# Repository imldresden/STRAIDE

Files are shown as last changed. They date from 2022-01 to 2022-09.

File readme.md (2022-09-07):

# STRAIDE: A Research Platform for Shape-Changing Spatial Displays based on Actuated Strings

**[Severin Engert](https://imld.de/en/our-group/team/severin-engert/), [Konstantin Klamka](https://imld.de/en/our-group/team/konstantin-klamka/), [Andreas Peetz](https://imld.de/en/our-group/team/andreas-peetz/), [Raimund Dachselt](https://imld.de/en/our-group/team/raimund-dachselt/)**

**[Interactive Media Lab Dresden](https://imld.de/en/)**

## CHI'22 Full Paper

We present STRAIDE, a string-actuated interactive display environment that allows to explore the promising potential of shape-changing interfaces for casual visualizations.
At the core, we envision a platform that spatially levitates elements to create dynamic visual shapes in space.
We conceptualize this type of tangible midair display and discuss its multifaceted design dimensions.
Through a design exploration, we realize a physical research platform with adjustable parameters and modular components.
For conveniently designing and implementing novel applications, we provide developer tools ranging from graphical emulators to in-situ augmented reality representations. 
To demonstrate STRAIDE's reconfigurability, we further introduce three representative physical setups as a basis for situated applications including ambient notifications, personal smart home controls, and entertainment.
They serve as a technical validation, lay the foundations for a discussion with developers that provided valuable insights, and encourage ideas for future usage of this type of appealing interactive installation.

[doi.org/10.1145/3491102.3517462](https://doi.org/10.1145/3491102.3517462)

## Repository
maintained by [Severin Engert](https://github.com/sev01)

### Components:
* [Hardware](Hardware)
* [Firmware](Firmware)
  * [Server](Firmware/Server_NodeJS)
  * [Slave Motors](Firmware/Motor_Uno)
  * [Slave Colors](Firmware/Color_ESP32)
* [Software](Software)
  * [Platform Emulator](Software/PlatformEmulator) ([Executable](Software/PlatformEmulator/PlatformEmulator.zip), [Unity-Project](Software/PlatformEmulator/Unity), AR (tba))
  * [Clients](Software/Clients) ([Arduino](Software/Clients/Arduino), [JavaScript](Software/Clients/), [C#](Software/Clients/Unity))
  * [Visual Editor](Software/VisualEditor) (live (tba))

## Contributors

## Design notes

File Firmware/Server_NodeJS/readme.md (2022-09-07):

# NodeJS Server

The central heart of STRAIDE is a NodeJS server. It handles all the communication between the Motor Towers, the Color Clients, and any application. It opens 3 separate interfaces: a TCP server on port 7778 for the communication via Ethernet with the Arduino Unos, a WS server on port 7779 for the wireless communcation with any hardware components like the color clients, and the external WS interface for applications on port 7777.
For every Motor Tower/TCP client that opens a connection to the server, it creates a new class of `Tower` including four `Elements` that handle the movement (speed, acceleration, shutdown) of the physical elements. Applications connected to the WS interface can send command according to the [Protocol](../../Hardware/protocol.md) which will control those parameters.
A loop will regularly check for changes and send out new values to the assigned Motor Tower.

## Setup
Install `NodeJS` and `npm` on a capable machine, preferable a thin client like a Raspberry Pi 4B. Then connect the machine to a local network containing all the Motor Towers via Ethernet or WiFi. Disable any other connection interface, as the server will pick the first one available. Configure your router so that your machine receives a static IP address, copy this address to the [Motor_Uno](../Motor_Uno) firmware. Finally, run `npm install` and `node controller.js` to start the server and make sure, all three interfaces are properly connected.

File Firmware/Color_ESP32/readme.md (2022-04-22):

# Color Controller

STRAIDE's Matrix Setup uses 64 illuminated elements for appealing visualizations in midair.
Each element features a single SK6812 LED for individual illumination.
All LEDs are connected to a central PCB in the lower Display Element Unit via 3m long tone arm wires.
8 LEDs make up a column, and overall 8 columns are connected to 8 digital pins of an NodeMCU ESP32.
This wifi-capable microcontroller connects to the central server and receives websocket messages containing new color information.
These are repeatedly send to the 8 strains of LEDs, and (with low latency) color works in unison with the actuation of the spheres.

## Message Format
`messageType | messageID | LED0 red | LED0 green | LED0 blue | LED0 white | LED1 red | LED1 green | ...`

`messageType`: `0x01` for new colors  
`messageID`: sequential numbers `0-255`  
LED: `index = y * DIMX + x` and `red`(byte)

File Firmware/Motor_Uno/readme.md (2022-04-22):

# Motor Controller

STRAIDE setups comprise multiple actuation towers, each with 4 motors and a PCB stack on top.
It is a stack of an Arduino Uno, an Ethernet Shield, a custom PCB to reroute pins, and an CNC Shield.
The Uno runs the software from this folder.
It uses the Ethernet Shield to connect to a network and WebSockets to connect to the central server.
Commands are mapped to the motor positions, including setup, calibration, and handling of direct user input.

## Setup
In `defines.h`, you need to adjust the `SLAVE_ADDR` for each individual actuation tower. Also, the `IPAddress serverIP(X.X.X.X)` and `IPAddress clientIP(X.X.X.X)` needs to be set up to fit the network.

## Communication
Element Position: `0x30 | messageID | M0 (high) | M0 (low) | M1 (high) | M1 (low) | M2 (high) | M2 (low) | M3 (high) | M3 (low)` (positions for each motor `M`: `high<<8+low`) 

Parameter: `0x20 | ParamID | high | low` (ParamID: `0x01`-speed, `0x02`-acceleration)

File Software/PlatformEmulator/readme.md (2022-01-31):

# Platform Emulator

The **Platform Emulator** can be used to test your applications. It emulates the full device and its behavior. Upon start, the application sets up a WebSocket server, that can be accessed from the same device or the local network. It will take and answer all incoming messages just like the original device (only low-level communication). The resultant behavior of the device is instantly visible. Use it to test your application before trying it on the real SCI.

The Platform Emulator can either be started as a standalone [Application](PlaformEmulator.zip) or opened as a [Unity Project](Unity).

## Application
The _Application_ folder contains a Windows Standalone **Simulator.exe** that can be executed. The Platform Emulator should start as a windowed application, which can be adjusted to your setup.

**Common Problems:**

1. The application sets up a WebSocket server on the localhost of your system with port 7777. If this address is already taken, the server will throw an error and the application will not start properly.
2. If you want to access the WebSocket server from your local network, the address with the assigned port needs to be accessible. Windows Firewall tends to block unknown ports. More information on how to set up inbound and outbound rules for Windows Firewall can be found [here](https://www.tomshardware.com/news/how-to-open-firewall-ports-in-windows-10,36451.html). To check for errors, run `netstat -an` in the Windows PowerShell and check for existing connections with port 7777, like 0.0.0.0:7777, _yourIP_:7777, or ::::7777.

## Unity Project
The **Unity** folder contains the full Unity project for the Platform Emulator. You should start the Unity Hub and add the folder to your projects. Select a fitting Unity Version (currently 2020.1.11f1) and open the project. The Platform Emulator can be run directly from the Unity Editor. WebSocket Server or Port problems are less common, as they are tunneled through the Unity ports 50XXX.

# Functionality
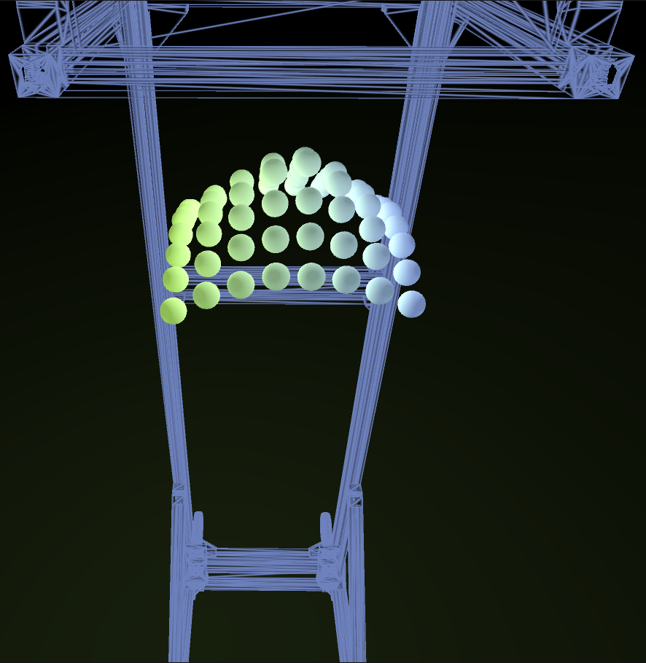
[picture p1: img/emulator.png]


The core of the Platform Emulator is the digital model of the device with its 64 spheres. Their position and color relate to the current state of the SCI which can be altered by incoming messages.

**Limitations:**
- speed parameter is approximated, slow speeds use workaround with jitter
- color rendering might be different than with the original device

## Controls
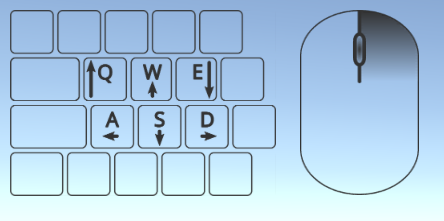
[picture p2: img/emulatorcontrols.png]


The space around the display can be navigated by using the WASD keys to move around, the QE keys to move up and down, the scroll wheel to zoom and the left mouse button to look around.

Further keys used as follows:<br/>
1,2,3,4,5 - predefined camera positions<br/>
0 - toggle frame<br/>
P - pick display<br/>
L - toggle light<br/>
O - toggle strings<br/>
ESC - exit application

## Interaction
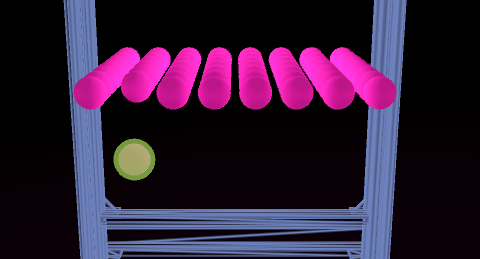
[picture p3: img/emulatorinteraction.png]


By hovering the mouse above an outer non-moving element, it gets selected. The position of a selected element can be manually altered using the primary mouse button.

## Strings
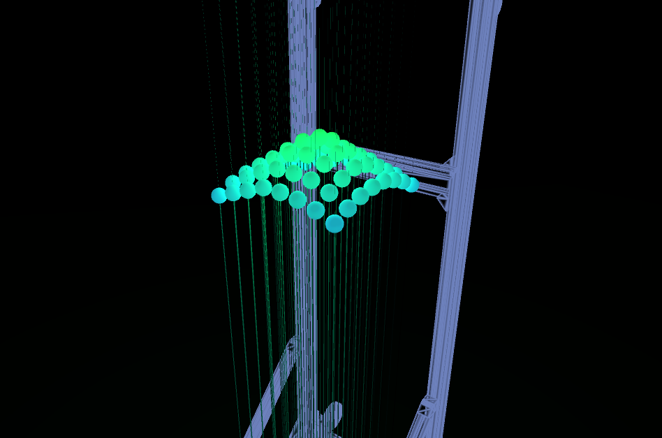
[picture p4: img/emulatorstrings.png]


Using the **O** key, strings and cables can be toggled. They are connected to each element and move in accordance, although applied line renderer is a bad approximation.

## Lights
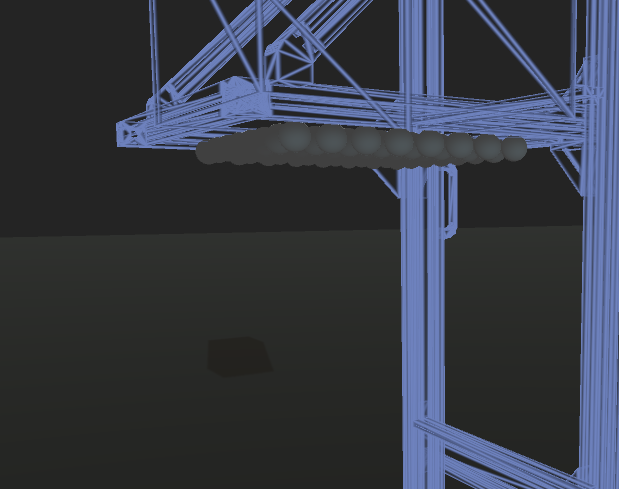
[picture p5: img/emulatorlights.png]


Using the **L** key, environmental light can be toggled for improved realism.

## Displays
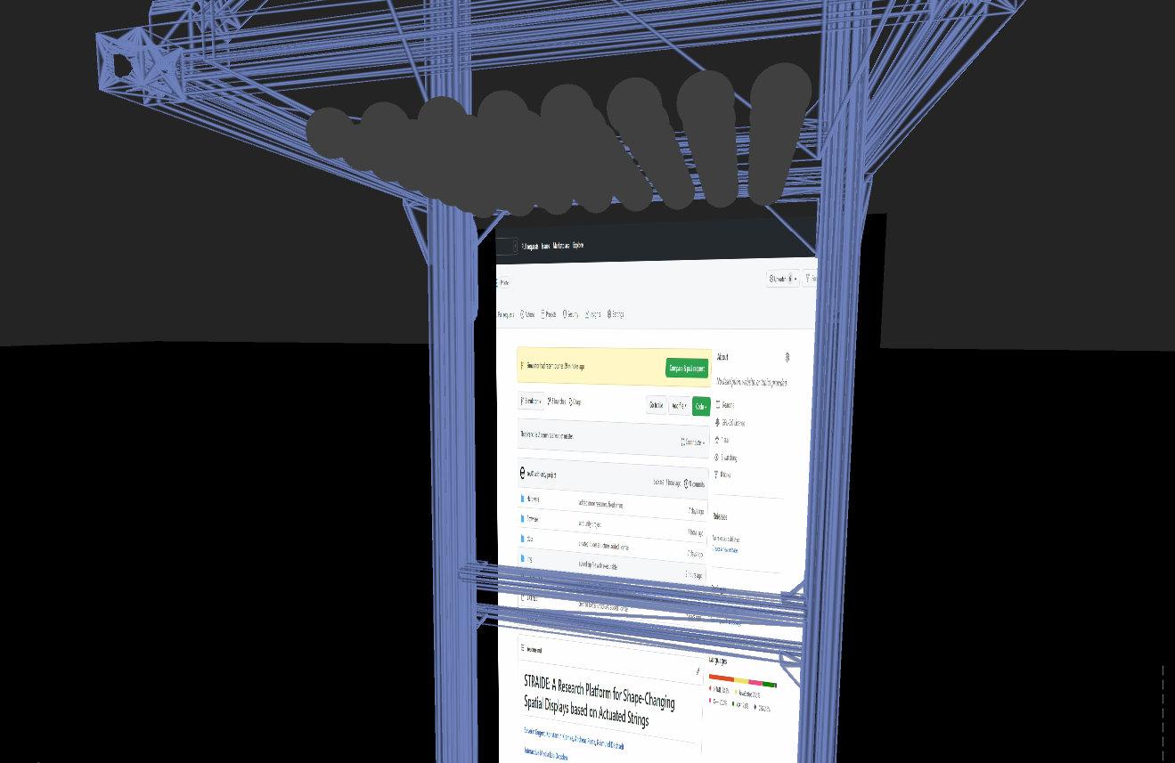
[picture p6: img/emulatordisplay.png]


For some applications, it was nice to have a background image or so inside the Platform Emulator. Therefore, it features multiple canvases to which a camera can be streamed, most often used with a virtual cam transferring parts of the screen. Use **P** to toggle the canvas.

## Supplementaries
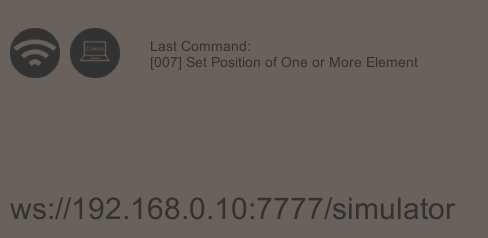
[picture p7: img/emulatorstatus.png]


Status information is displayed in the lower part of the screen.
The first icon shows the Platform Emulators connectivity. The second icon shows whether a client is connected or not. On its right, the last inbound command is displayed according to the message's ID. To learn more about the messages, see [Protocol](../../Hardware/protocol.md).
The empty space underneath the icons is filled with log/error messages, as they occur. This can be used for Debug purposes, e.g. a warning is displayed if an inbound message had the wrong length or format.

In the lower-left corner, the address of the WebSocket server is displayed. It needs to be entered into the SCIClients address field.

The lower-right corner shows the target position values for all 64 elements.

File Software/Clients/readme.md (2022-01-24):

# STRAIDE Client Libraries

To simplify the application development for STRAIDE on various platforms, we implemented client libraries in different programming languages (JS, C#, C++).They provide functions for establishing connections and setting the properties of elements, as well as events for system state changes and user input.

For further details, please take a look into the individual folders:
* [JavaScript](JS)
* [C# (for Unity)](Unity)
* [C++ (for Arduino)](Arduino)

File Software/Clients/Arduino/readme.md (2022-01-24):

# Arduino Client

This _SCIClient_ is intended to be used on ESP32 micro-controller boards that should communicate with STRAIDE, e.g., for IoT applications

## Setup

To use the SCIClient in a script, you should create a new library. Open the Arduino [Library](https://www.arduino.cc/en/Guide/Libraries) folder and create a new folder called _SCIClient_. Copy the `SCIClient.h` and `SCIClient.cpp` files into this folder. Now you need to import the library in your sketch.

The library uses the [Arduino WebSocket](https://github.com/Links2004/arduinoWebSockets) library. Make sure, the library is ready for import aswell. 

Create a new SCIClient object as a global variable with the correct address information. In your script's `setup()` function, you should setup a WiFi connection and register a callback that is triggered when the WebSocket server is ready. Use this call to request information that is needed for your application.

```cpp
#include <SCIClient.h>

SCIClient client = SCIClient("192.168.0.1", 7777, "/simulator");  // for Simulator
// SCIClient client = SCIClient("10.6.0.1", 7777, "/");  // for real STRAIDE

void setup(){
   WiFi.mode(WIFI_STA);
   WiFi.begin(WLAN_SSID, WLAN_PASS);
   client.CallOnReady(ServerIsReady);
}

void ServerIsReady(){
   sciclient.GetInformation(SCIClient::InfoID::DIM);
}
```

## Ping
Send a simple ping to the device.
```cpp
sciclient.SendPing();
```

## Acknowledgments
Typically, STRAIDE will send acknowledgment packets `0x01 | MessageID` for every received data packet. To reduce the traffic, acknowledgments can be toggled by sending:
```cpp
sciclient.ToggleAcknowledgment(false);
```

## Reset
To reset STRAIDE or some parts thereof send
```cpp
sciclient.Reset(0x00);
```
The code determines what to reset:\
`0x00` - Reset Everything\
`0x01` - Reset Elements' Positions (aka calibrate positions)\
`0x02` - Reset Elements' Color (aka turn off all lights)

## Request Information
For many client applications it is necessary to know some information about STRAIDE. The `InfoID` defines all potential information that can be requested. Currently it supports `DIM, DIAMETER, RESOLUTION, STEPSPERM, MAXSTEPS`.

```cpp
sciclient.GetInformation(SCIClient::InfoID::DIM);
```
To receive the requested information, you need to register a custom callback function. Take a look into the [Protocol](/Hardware/protocol.md) to find the encoding of the response's data.
```cpp
int maxsteps = 0;
void RequestInformation(){
   sciclient.CallOnInfo(ReceiveInformation);
   sciclient.GetInformation(SCIClient::InfoID::MAXSTEPS);
}

private void ReceiveInformation(byte[] data){
   switch(data[0]){
      case SCIClient::InfoID::MAXSTEPS:
         maxsteps = (int)word(data[1], data[2]);
         break;
   }
}
```

## Set Parameter
To set a motor parameter of STRAIDE (see [Parameters](/Hardware/parameters.md)), use
```cpp
sciclient.SetParam(SCIClient::ParamID::SPEED, 1000);
```
The `SCIClient::ParamID` currently defines `SPEED, ACCELERATION`.

## Set Position
The API provides three ways to set the position of elements. To set the position of a single element, use
```cpp
sciclient.SetElementPosition(new SCIElement(2,5), 4321);
```

To set multiple elements (in a rectangular region defined by the coordinates of the lower left and upper right corner elements) to the same position, use
```cpp
sciclient.SetAreaPosition(new SCIElement(2,3), new SCIElement(4,6), 4321);
```

To set the position of all elements individually, use
```cpp
sciclient.SetMultiplePositions(positions, 64);   // int positions[64]; 
```
The array needs to have a length of exactly `XDimension * YDimension`. To properly sort the elements' positions, calculate `i = y * XDimension + x` for each element. The second parameter needs to be the length of the array.

## Set Color
The API provides three ways to set the color of elements. A basic definition for colors is provided by the `SCIColor` class. To set the color of a single element, use
```cpp
sciclient.SetElementColor(new SCIElement(2,5), new SCIColor(255,0,0));
```
To set multiple elements (in a rectangular region defined by the coordinates of the lower left and upper right corner elements) to the same color, use
```cpp
sciclient.SetAreaColor(new SCIElement(2,3), new SCIElement(4,6), new SCIColor(255,0,0));
```

To set the color of all elements individually, use
```cpp
sciclient.SetMultipleColors(colors, 64);   // SCIColor colors[64];
```
The array needs to have a length of exactly `XDimension * YDimension`. To properly sort the elements' positions, calculate `i = y * XDimension + x` for each element.

## Set Position and Color
To reduce the WebSocket traffic, messages can combine position and color definitions for one or multiple elements. 
```cpp
sciclient.SetPositionAndColor(new SCIElement(2,5), 4321, new SCIColor(255,0,0));

sciclient.SetAreaPositionAndColor(new SCIElement(2,3), new SCIElement(4,6), 4321, new SCIColor(255,0,0));

sciclient.SetMultiplePositionsAndColors(positions, colors);
```

## Animations
Some animations are predefined on STRAIDE itself. Currently, this includes different sine waves. Each animation has an ID (currently ranging from 0-5). To start or change an animation, use
```cpp
sciclient.PlayPreset(2);
```
Animations can be stopped by sending any command that sets the positions of at least one element.

The amplitude of the predefined sine waves is approximately 20cm. But the vertical position of the sine wave can be adapted by using
```cpp
sciclient.SetOffset(4321);
```

## User Input
Users can manually drag the outer elements of the device. The respective data is send to all clients via the WebSocket broadcast method. Register a custom method using `CallOnInput(method)` to access the data. The method should take an `SCIElement` and an integer value as parameters like this:

```cpp
sciclient.CallOnInput(UserInput);

private void UserInput(SCIElement element, int value){
   // element.x and element.y available
   // value: absolute steps from top for respective element
}
```

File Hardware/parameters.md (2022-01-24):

# Controllable Motor Parameters

To date, STRAIDE applications can control 2 different parameters of the actuators.

## Speed
The speed for each motor can be defined as an unsigned integer value. It refers to the number of steps per second, which the stepper motor actuates the elements. A single step size can be calculated as

$step=pi*40mm/400\approx0.31416mm$

The real world speed can therefor be calculated like

$RealSpeed=speed*^{step}/_s$

| Speed | RealSpeed |
| --- | --- |
| 100 | $`31^{mm}/_s`$ |
| 1000 | $`314^{mm}/_s`$ |
| 4000 | $`1257^{mm}/_s`$ |

The speed value can be picked in between $0-4000$. Everything above 4000 is not achievable due to hardware constraints. Everything above 1000 is only achievable, if only one of every 4 motors is actuated, as they are internally grouped into $2\times2$ motor towers. Speeds below 200 should be prevented, as the motor's torque is reduced at low speeds.

## Acceleration
***! Acceleration NOT yet implemented in Simulator !*** 

The acceleration is also defined as an unsigned integer value. It refers to the speed increase in steps per square second. Generally an acceleration above 1000 should be picked.

More information can be found in the chart. Currently, the elements weight approximately 200g.
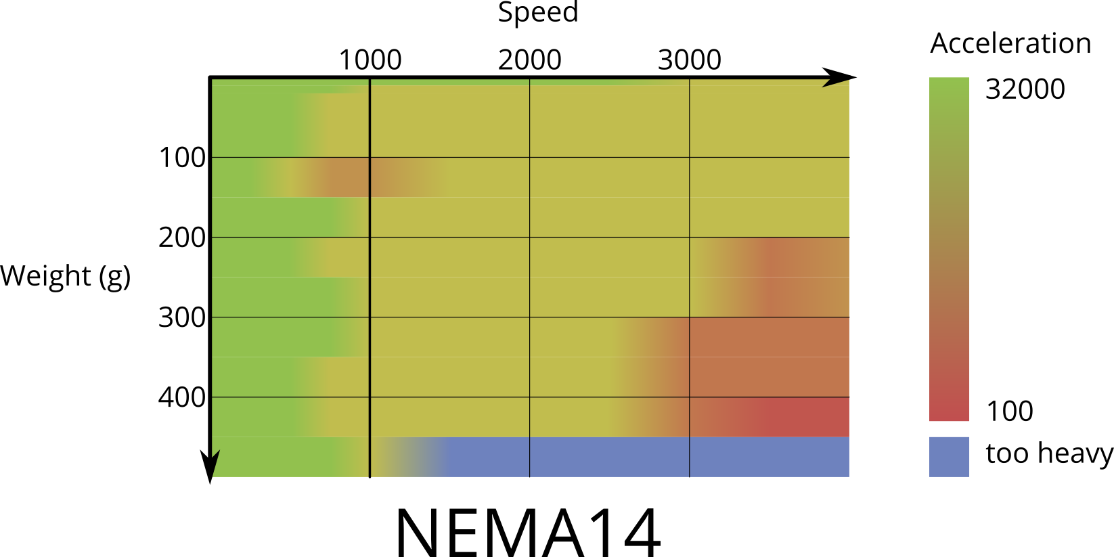
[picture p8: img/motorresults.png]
motorresults


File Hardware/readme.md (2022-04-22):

# STRAIDE Hardware

## License
Copyright Severin Engert 2022.

This source describes Open Hardware and is licensed under the CERN-OHL-S v2.
You may redistribute and modify this source and make products using it
under the terms of the [CERN-OHL-S v2](https://ohwr.org/cern_ohl_s_v2.txt).

This source is distributed WITHOUT ANY EXPRESS OR IMPLIED WARRANTY, INCLUDING OF MERCHANTABILITY, SATISFACTORY QUALITY AND FITNESS FOR A PARTICULAR PURPOSE. Please see the CERN-OHL-S v2 for applicable conditions.
Source location: [https://github.com/imldresden/STRAIDE](https://github.com/imldresden/STRAIDE)

As per CERN-OHL-S v2 section 4, should You produce hardware based on this source, You must where practicable maintain the Source Location visible on the external case of the STRAIDE or other products you make using this source.

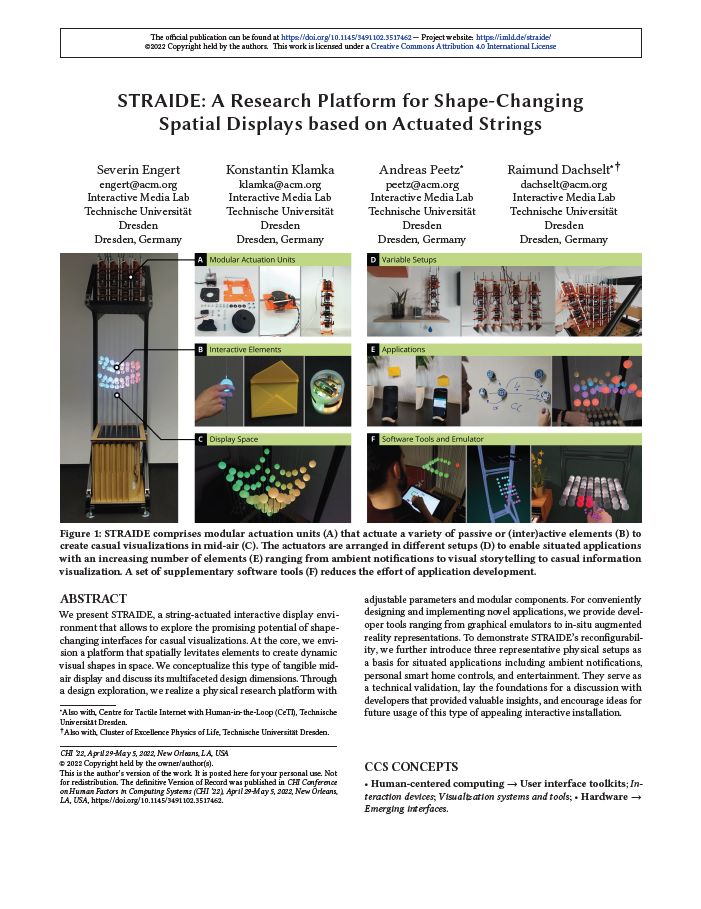
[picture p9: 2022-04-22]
docs/assets/img/full_paper.jpg

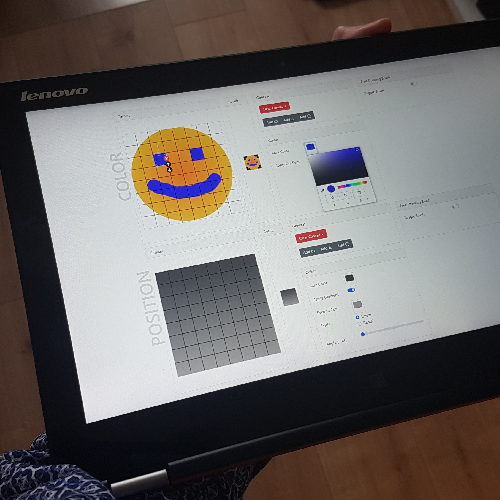
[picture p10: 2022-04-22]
docs/assets/img/visual_designer.png

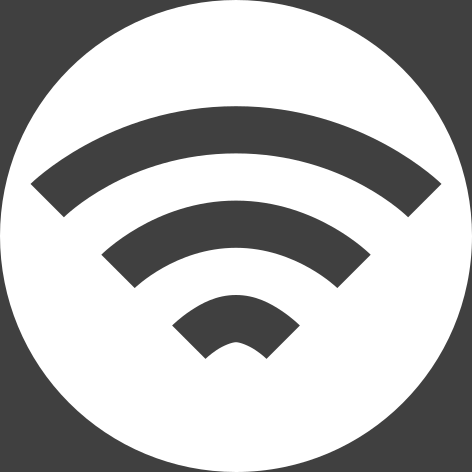
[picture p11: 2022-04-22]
Software/PlatformEmulator/Unity/Assets/Images/connected.png

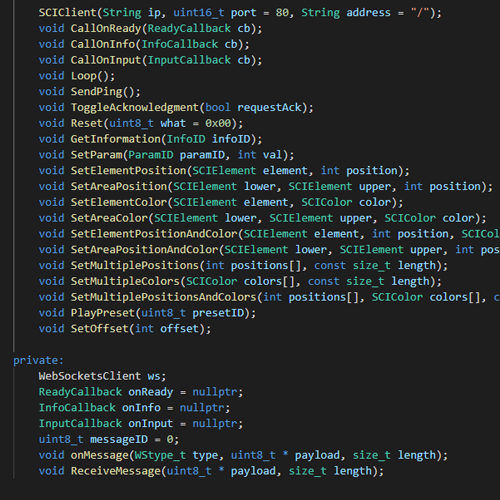
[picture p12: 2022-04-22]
docs/assets/img/clients.png

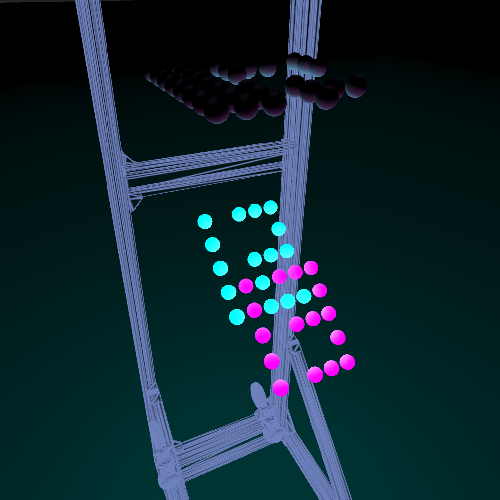
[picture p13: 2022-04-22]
docs/assets/img/emulator.png

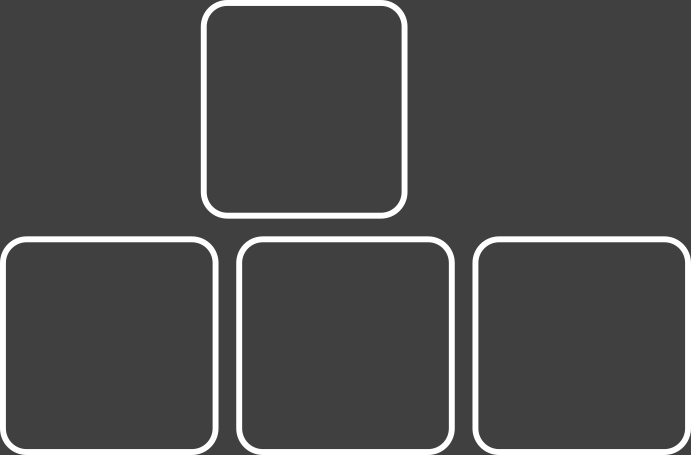
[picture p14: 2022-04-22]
Software/PlatformEmulator/Unity/Assets/Images/controls.png

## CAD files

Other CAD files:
Hardware/stl/Spool.stl
Software/PlatformEmulator/Unity/Assets/Frame.stl
Hardware/stl/EndStopHolder.stl
Hardware/Fusion360/BackCover.f3z
Hardware/Fusion360/ControllerMount.f3z
Hardware/Fusion360/LuffTackle.f3d
Hardware/Fusion360/MotorMount.f3z
Hardware/Fusion360/UpperCover.f3z

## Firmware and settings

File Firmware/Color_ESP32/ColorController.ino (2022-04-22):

#include <Adafruit_NeoPixel.h> // install library from https://github.com/adafruit/Adafruit_NeoPixel
#include <WiFi.h>              // part of esp-32 arduino library https://github.com/espressif/arduino-esp32
#include <confidential.h>      // private libray containing WLAN_SSID and WLAN_PASS
#include <WebSocketsClient.h>  // install library from https://github.com/Links2004/arduinoWebSockets

#define IP "X.X.X.X" // enter the IP of server

#define LEDS_PER_ROW 8

#define ROW_0_PIN 14
#define ROW_1_PIN 27
#define ROW_2_PIN 26
#define ROW_3_PIN 25
#define ROW_4_PIN 33
#define ROW_5_PIN 32
#define ROW_6_PIN 16
#define ROW_7_PIN 17

WebSocketsClient ws;

Adafruit_NeoPixel leds0(LEDS_PER_ROW, ROW_0_PIN, NEO_GRBW + NEO_KHZ800);
Adafruit_NeoPixel leds1(LEDS_PER_ROW, ROW_1_PIN, NEO_GRBW + NEO_KHZ800);
Adafruit_NeoPixel leds2(LEDS_PER_ROW, ROW_2_PIN, NEO_GRBW + NEO_KHZ800);
Adafruit_NeoPixel leds3(LEDS_PER_ROW, ROW_3_PIN, NEO_GRBW + NEO_KHZ800);
Adafruit_NeoPixel leds4(LEDS_PER_ROW, ROW_4_PIN, NEO_GRBW + NEO_KHZ800);
Adafruit_NeoPixel leds5(LEDS_PER_ROW, ROW_5_PIN, NEO_GRBW + NEO_KHZ800);
Adafruit_NeoPixel leds6(LEDS_PER_ROW, ROW_6_PIN, NEO_GRBW + NEO_KHZ800);
Adafruit_NeoPixel leds7(LEDS_PER_ROW, ROW_7_PIN, NEO_GRBW + NEO_KHZ800);
Adafruit_NeoPixel *rows[64 / LEDS_PER_ROW];

bool dirty[] = {false, false, false, false, false, false, false, false};

void setup()
{
    Serial.begin(115200);

    // Setup WiFi
    WiFi.mode(WIFI_STA);
    WiFi.begin(WLAN_SSID, WLAN_PASS);

    while (WiFi.status() != WL_CONNECTED)
    {
        delay(500);
        Serial.print(".");
        if (millis() > 20000) // sometimes this process takes forever, ESP32 can be restarted which sometimes helps, remove for other microcontrollers
            ESP.restart();
    }

    // Setup WS connection
    ws.begin(IP, 7779, "/");
    ws.onEvent(onMessage);
    ws.setReconnectInterval(5000);

    // Setup LEDs
    rows[0] = &leds0;
    rows[1] = &leds1;
    rows[2] = &leds2;
    rows[3] = &leds3;
    rows[4] = &leds4;
    rows[5] = &leds5;
    rows[6] = &leds6;
    rows[7] = &leds7;

    for (Adafruit_NeoPixel *leds : rows)
    {
        leds->begin();
        leds->show();
        leds->setPixelColor(0, leds->ColorHSV(random(64000), 255, 150));
        for (int i = 1; i < LEDS_PER_ROW; i++)
        {
            leds->setPixelColor(i, leds->Color(0, 0, 0));
        }
        leds->show();
    }
}

// Loop WS and apply new colors to LEDs
void loop()
{
    for (int i = 0; i < 8; i++)
    {
        if (dirty[i])
        {
            delay(1);
            portDISABLE_INTERRUPTS(); // sometimes color flickering occurs due to interrupt handling, this might be workaround
            rows[i]->show();
            portENABLE_INTERRUPTS();
            dirty[i] = false;
        }
    }
    ws.loop();
}

void dataAvailable(uint8_t *payload, size_t length)
{
    if (length == 2 + 64 * 4)
    {
        for (uint8_t x = 0; x < 8; x++)
        {
            Adafruit_NeoPixel *leds = rows[x];
            for (uint8_t y = 0; y < 8; y++)
            {
                int i = y * 8 * 4 + x * 4 + 2;
                uint32_t col = leds->gamma32(leds->Color(payload[i], payload[i + 1], payload[i + 2], payload[i + 3]));
                if (leds->getPixelColor(y) != col)
                {
                    leds->setPixelColor(y, col);
                    dirty[x] = true;
                }
            }
        }
    }
    else
    {
        Serial.println("Received malformed data.");
    }
}

void onMessage(WStype_t type, uint8_t *payload, size_t length)
{
    switch (type)
    {
    case WStype_DISCONNECTED:
        Serial.printf("[WS] Disconnected!\n");
        break;
    case WStype_CONNECTED:
        Serial.printf("[WS] Connected to url: %s\n", payload);
        break;
    case WStype_TEXT:
        break;
    case WStype_BIN:
        dataAvailable(payload, length);
        break;
    case WStype_ERROR:
    case WStype_FRAGMENT_TEXT_START:
    case WStype_FRAGMENT_BIN_START:
    case WStype_FRAGMENT:
    case WStype_FRAGMENT_FIN:
        break;
    }
}

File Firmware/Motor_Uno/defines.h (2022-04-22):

#pragma once

#include <AccelStepper.h>
#include <MultiStepper.h>
#include <SPI.h>
#include <Ethernet.h>

#define SLAVE_ADDR 17
#define RETRACTION 5
#define DEBUG false

// Pin Assignment with Ethernet Shield
#define ETH_EN A5

#define EN_PIN 8
#define MOTOR1_STEP A2
#define MOTOR1_DIR A4
#define MOTOR2_STEP 4
#define MOTOR2_DIR 7
#define MOTOR3_STEP 2
#define MOTOR3_DIR 5
#define MOTOR4_STEP 3
#define MOTOR4_DIR 6

#define USE_ENDSTOPS true
#define ANTI_CLOCKWISE false
#define MOTOR1_STOP A3
#define MOTOR2_STOP A1
#define MOTOR3_STOP 9
#define MOTOR4_STOP A0

#include "SCIMotor.h"

// Communication Messages
enum MessageType {
    PING = 0x00,
    CONFIRM = 0x01,
    SETPARAM = 0x20,
    ELEMENTPOS = 0x30
};

enum ParamID {
    SPEED = 0x01,
    ACCELERATION = 0x02
};

// Ethernet setup
byte mac[] = {0xFC, 0xFE, 0xFE, 0xFE, 0xFE, SLAVE_ADDR};
IPAddress clientIP(X, X, X, SLAVE_ADDR);
IPAddress serverIP(X, X, X, X);
const int serverPort = 7778;

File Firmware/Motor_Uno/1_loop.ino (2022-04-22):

#include "defines.h"

// loop ethernet and all motors
void loop()
{
  int i = 0;
  for (SCIMotor *m : motors)
  {
#if DEBUG == true
    if (i == 0)
    {
      Serial.print(3000);
      Serial.print(",");
      Serial.print(m->m()->currentPosition());
      Serial.print(",");
      Serial.print(m->m()->targetPosition());
      Serial.print(",");
      Serial.print(m->m()->speed() + 2500);
      Serial.print(",");
      Serial.println(2000);
      i++;
    }
#endif
    m->run();
  }
  loopEthernet();
}

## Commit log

2022-01-31 add unity project
    [Frame.stl]
2022-02-15 added code for the motor controllers with comments and readme
2022-04-22 added most hardware files: stl, svg, gerber, f3z
    [BackCover.f3z, ControllerMount.f3z, EndStopHolder.stl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]
2022-04-22 linked hardware files in BOM
